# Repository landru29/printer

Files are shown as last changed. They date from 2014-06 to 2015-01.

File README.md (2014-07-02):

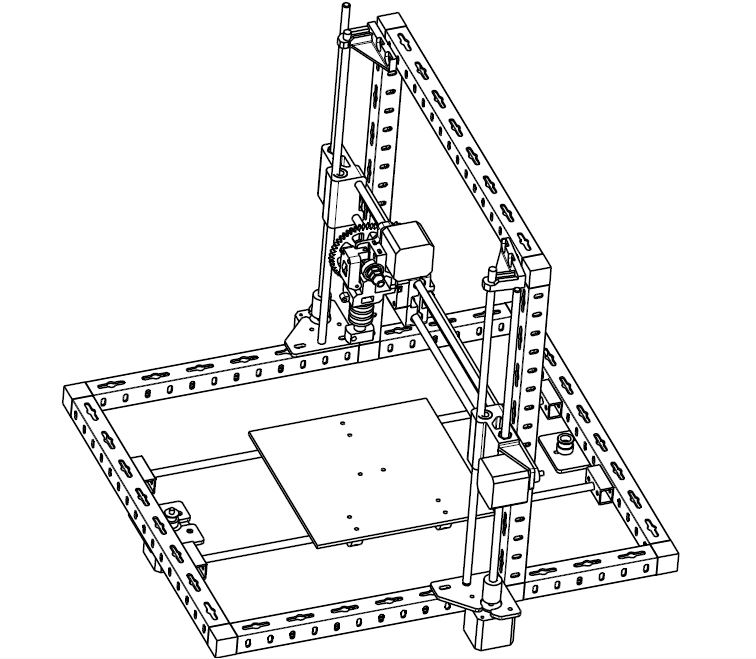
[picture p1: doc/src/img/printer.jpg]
Imprimante 3D


Cadre du projet
===============
Une imprimante 3D est une machine qui permet de reproduire des pièces plus ou moins complexes par apport de matière. Il existe plusieurs types d'imprimantes, selon le principe d'apport de matière utilisé. Le prérimètre de ce projet est une imprimante qui extrude du plastique à déposer couches par couches.

Objectif
========
Le principal objectif est, évidement, de construire une imprimante 3D. Cette imprimante fonctionnera sur le principe d'extrusion de matière plastique. Je m'appuie sur les imprimantes Reprap http://reprap.org/wiki/RepRap/fr. Dans cette perspective, je m'autorise à réutiliser, modifier, adapter des pièces conçues pour d'autres imprimantes Reprap.
Une contrainte forte de ce projet est le budget. En référence, une imprimante Reprap i3 en kit est vendue 450€ sans l'électronique de commande (600€ tout compris). Mon objectif est de limiter mon budget à 250€. C'est difficilement atteignable, mais pas impossible.

Les imprimantes RepRap
======================
Le principe de ces imprimantes est qu'elles sont réplicables. Concrêtement, pour fabriquer une imprimante RepRap, on profite d'une autre imprimante pour imprimer des pièces. Mon projet repose sur ce principe. En effet, pour des questions de facilité (je m'affranchis de certains usinages complexe), la plupart des supports seront imprimés.

Organisation du projet
======================
On trouve deux dossiers:
> * `doc` (documentation du projet, source LaTeX)
> * `mecanical` (conception mécanique du projet)

Doc
---

La documentation est écrite en LaTeX. Pour la regénérer il faut "compiler" les sources. Certaines extensions sont nécessaire à la construction du document (tous ces dépendances se trouvent dans le fichier `doc/source/printer.tex`).
Chaque chapitre a sont propre fichier `*.tex` pour plus de facilité à la rédaction. Un `Makefile` (et un `make.bat`) est à disposition pour faciliter la compilation

Mecanical
---------
Vous trouverez les différents éléments:
> * Les pièces qui devront être imprimées sont dans le dossier `mecanical/to_print`.
> * Les sous-ensembles constituant l'imprimante sont dans `mecanical/assembly`.
> * L'imprimante complete se trouve à la racine de `mecanical`.
> * La bibliothèque de roulement à billes est dans `mecanical/bearing`
> * Les éléments de la structure sont dans `mecanical/tubes`
> * La pré-étude de la tête d'extrusion est dans `mecanical/head`
> * Toute la quincaillerie standard est dans `mecanical/standard`

Attention, il arrive que j'oublie de mettre à jour les fichiers `*.stl` (que je maintiens uniquement pour la visionneuse de GitHub). Vérifiez bien les dates !

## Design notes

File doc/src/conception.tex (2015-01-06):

\section{Conception}
\subsection{Le chassis}
Le chassis est en profile aluminum. Plusieurs solutions se sont %
présentées :\begin{dinglist}{71}%
\item{utiliser du profile pour la construction modulaire}%
\item{utiliser du profile carré}%
\item{utiliser les profiles que propose une célèbre enseigne française %
blanche et verte (fig. \ref{profile} page~\pageref{profile})}
\end{dinglist}%
\par%
\begin{figure}%
   \caption{\label{profile} Profile aluminium 23.5 x 23.5}
   \center{}
\end{figure} %
La première solution est chère. Il faut compter 60\euro{} les trois mètres %
(30mm), sans compter la quincaillerie d'assemblage. \par%
La seconde solution, la moins chère, est plus difficile à mettre en %
oeuvre et nécessite de la précision dans les usinages (perçages, sciages, %
...) pour avoir de bons alignements.\par%
La dernière solution est un bon compromis, car c'est une solution de %
construction modulaire à petit prix (15\euro{} les 2,5m x 25mm). Les jonctions %
se font avec des L et des T en PVC. Si ce n'est pas assez rigide, je %
pourrais encore ajouter des équerres métaliques.
\subsection{L'électronique}
\subsubsection{Spécification}
L'électronique de commande doit respecter les spécifications suivantes: %
\begin{dinglist}{71}%
\item{Elle devra piloter 5 axes (1 X-axis, 1 Y-axis, 2 Z-axis, 1 extrudeur)} %
\item{Elle se connectera à un ordinateur via le port USB} %
\item{Elle supportera une carte SD pour l'imprimante soit autonome lors de %
l'impression} %
\item{Elle saura piloter des moteurs pas à pas bipolaires}
\item{Elle intégrera les différents capteurs (fin de course, température de %
l'extrudeur)}
\item{Elle saura piloter le partie chauffante de l'extrudeur} %
\item{Elle ne sera pas propriétaire} %
\end{dinglist} %
\subsubsection{La Smoothieboard}
Toujours, pour des questions de budget, j'ai écarté la solution Smoothie %
(http://smoothieware.org/smoothieboard). Il faut compter 125\euro{} pour une %
carte 5 axes.
\subsubsection{Arduino}
La solution Arduino consiste à utiliser la version Mega et y brancher une carte %
de commande de moteur. Je suis donc parti sur la configuration suivante: %
\begin{dinglist}{71}%
\item{Freeduino 2650 Mega (un clone de l'Arduino, mais en moins cher): 19\euro}%
\item{RAMPS (une carte de commande de moteur; la plus utilisée par les firmwares %
proposés): 14\euro}%
\item{5 modules A4988 (commande de moteur pas à pas) avec radiateur: 5\euro{} chacun}
\end{dinglist}%
%
\subsection{Liste du matériel}
\csvreader[tabular=|l|l|l|r|,
    table head=\hline & Description & Qte & Prix\\\hline,
    late after line=\\\hline]%
{bom.csv}{Description=\Description,Qte=\Qte,Prix=\Prix}%
{\thecsvrow & \Description & \Qte & \Prix}%
%
\subsection{la tête d'impression}
\noindent Fig. \ref{sch_tete} page~\pageref{sch_tete} \par %
\begin{figure}%
   \caption{\label{sch_tete} Dessin de la tête d'impression}%
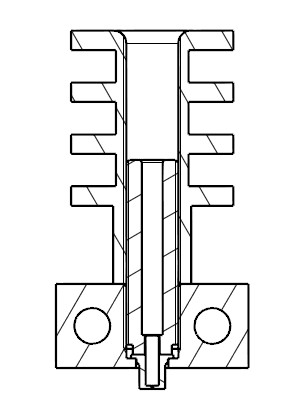
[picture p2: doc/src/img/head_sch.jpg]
   \center{}%
\end{figure}%
La tête d'impression est entièrement fabriquée (fig. \ref{tete_impression} %
page~\pageref{tete_impression}). Elle se compose de quatre éléments:%
\begin{dinglist}{71}%
\item{l'élément de chauffe (qui contiendra la résistance chauffante et la thermistance)}%
\item{le radiateur (qui refroidit la partie haute)}%
\item{le noyau en laiton(pour solidariser le radiateur et l'élément de chauffe)}%
\item{la buse (qui est une partie métalique percée à 0,2mm)}%
\end{dinglist}%
Un noyau en inox (mauvais conducteur thermique) viendra se visser au dessus de la tête.
\begin{figure}%
   \caption{\label{tete_impression} Tête d'impression}%
   \center{}%
\end{figure}%
\subsubsection{L'élément de chauffe}%
\noindent Fig. \ref{sch_chauffe} page~\pageref{sch_chauffe} \par %
\begin{figure}%
   \caption{\label{sch_chauffe} Dessin de l'élément de chauffage}%
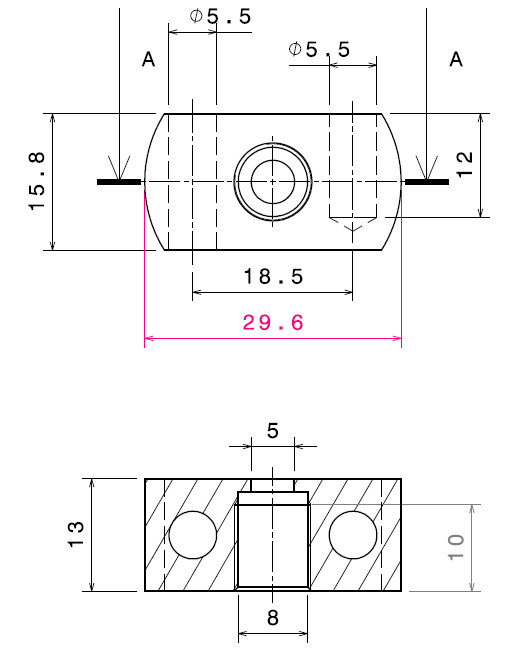
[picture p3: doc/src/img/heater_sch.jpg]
   \center{}%
\end{figure}%
La conception est assez simple. Il faut un bloc de métail (dans mon cas de l'aluminium), et %
percer un logement pour la résistance chauffante et un logement pour la thermistance.%
Pour des facilités d'usinage, je suis parti d'un rond d'aluminium que j'ai fraisé %
(fig. \ref{usinage_chauffe} page~\pageref{usinage_chauffe}).%
\begin{figure}%
   \caption{\label{usinage_chauffe} Usinage de l'élément de chauffage}%
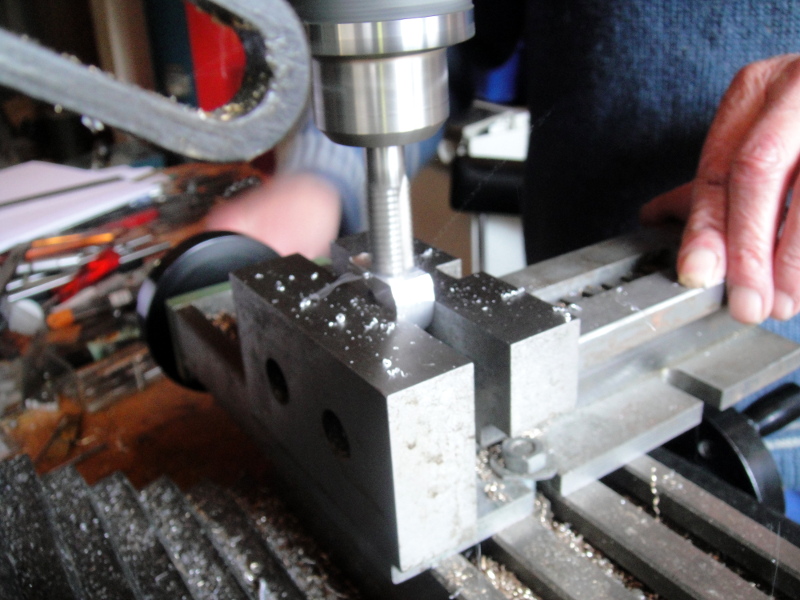
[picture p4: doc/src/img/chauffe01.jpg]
   \center{}%
\end{figure}%
\subsubsection{Le radiateur}%
\noindent Fig. \ref{sch_radiateur} page~\pageref{sch_radiateur} \par %
\begin{figure}%
   \caption{\label{sch_radiateur} Dessin du radiateur}%
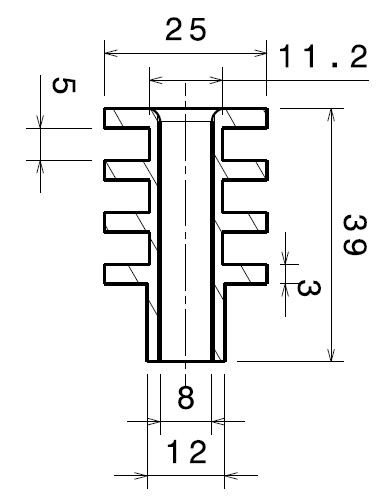
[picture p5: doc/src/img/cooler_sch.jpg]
   \center{}%
\end{figure}%
Cette pièce est aussi en aluminium. Avec un tour j'ai usiné des gorges pour faire les ailettes. %
Le perçage central est taraudé à M8 pour y visser le noyau (fig. \ref{usinage_radiateur} %
page~\pageref{usinage_radiateur}).%
\begin{figure}%
   \caption{\label{usinage_radiateur} Usinage du radiateur}%
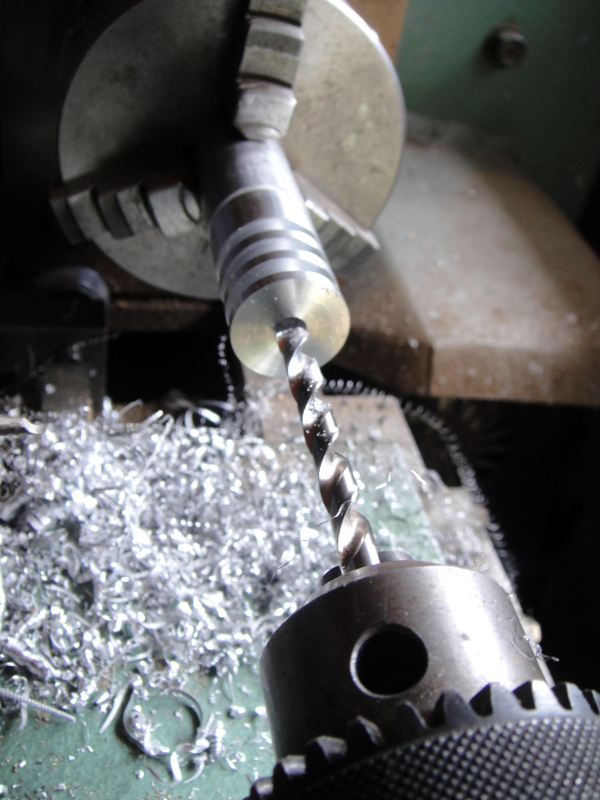
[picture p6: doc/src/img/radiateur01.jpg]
   \center{}%
\end{figure}%
\subsubsection{Le noyau}%
\noindent Fig. \ref{sch_noyau} page~\pageref{sch_noyau} \par %
\begin{figure}%
   \caption{\label{sch_noyau} Dessin du noyau}%
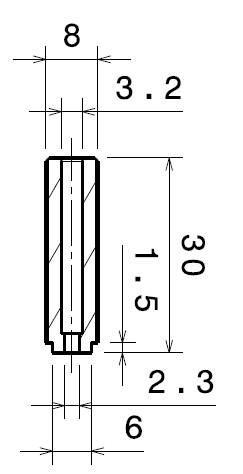
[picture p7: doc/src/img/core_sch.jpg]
   \center{}%
\end{figure}%
Le noyau est fabriqué à partir d'une tige fileté M8 en laiton. Cette pièce est percée à 3,2mm %
pour laisser passer le fil de plastique jusqu'à l'élément de chauffe.%
\subsubsection{La buse}%
Le choix de la buse a été assez difficile. La problématique est la suivante : où trouver %
une partie métallique percée à 0,3mm ou moins, pour pas cher ? \par%
Après renseignement, j'ai vite abandonné l'idée de percer moi-même. Les forêts de très petits %
diamètres sont chers et très fragiles (il faut faire des passes de 0,1mm). %
Je me suis rapidement orienté vers les injecteurs de cyclomoteurs ou de gaz. Les injecteurs de %
cyclomoteurs sont percés gros (minimum 0,6mm). Reste les injecteurs gaz. Chez un chauffagiste %
rennais (\url{http://www.jeanpaulguy.fr/contents/fr/p5656_SD_05447200.html}) j'ai trouvé un injecteur de veilleuse de chaudière murale à gaz (fig. \ref{buse} %
page~\pageref{buse}). C'est une petite pièce à moins de 2\euro{}, percée à 0,28mm ou 0,18mm (%
\url{http://www.jeanpaulguy.fr/contents/fr/p2629.html}).%
\begin{figure}%
   \caption{\label{buse} Buse d'extrusion}%
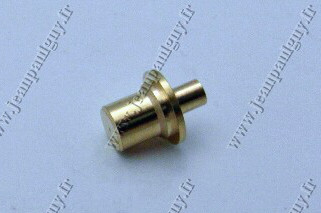
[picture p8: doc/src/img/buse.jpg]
   \center{}%
\end{figure}%
\subsection{La platine assemblée}%
\subsubsection{Fixation des glissières à billes}%
Les glissières à billes sont fixées serrées contre la platine. La fixation est usinée dans un premier temps par tournage, en alésant à 15mm un rond d'aluminium. %
La pièce passe ensuite sur le banc d'une fraiseuse pour réaliser les méplats. L'un des méplats sera tangent à l'alésage (en mangeant 0,3mm, pour assurer le serrage %
de la glissière contre la platine. Les perçages de fixation sont taraudés.
\begin{figure}%
   \caption{\label{bushing-bracket} Fixation de glissière à billes}%
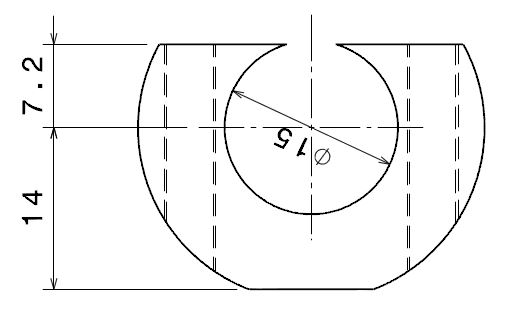
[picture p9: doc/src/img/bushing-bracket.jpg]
   \center{}%
\end{figure}%
\subsubsection{Fixation et contre-fixation de la courroie}%
Cette pièce est réalisée dans de l'aluminium de 6mm d'épaisseur (ce qui correspond à la largeur de la courroie). Pour créer les dentures, il suffit de percer à d1.5mm %
tous les 2mm (le pas de la courroie est de 2mm). Ensuite, scier le long de la ligne de perçage. On accentuera les dents en passant une lime triangulaire. Les %
perçages de fixation sont fraisurés. Le rayon de courbure de 5mm permet de limiter le frottement de la courroie (le retour risque d'être en contact).
\begin{figure}%
   \caption{\label{belt-blocker} Fixation de la courroie}%
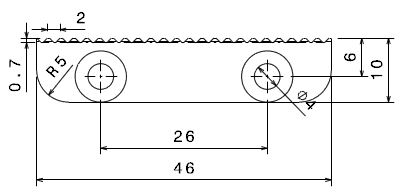
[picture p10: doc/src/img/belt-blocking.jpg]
   \center{}%
\end{figure}%
\subsubsection{Montage}%
Commencer par monter la fixation de courroie 2. Monter, sans serrer la contre-fixation 5. Loger les glissière dans leurs fixations et visser ces dernières sur la %
platine (sans trop serrer pour éviter l'hyperstatisme) avec des vis à têtes fraisurées. Il faudra reprendre la fixation des glissières lorsque la platine sera montée %
sur les stubs (barres de glissement).
\begin{figure}%
   \caption{\label{plate-assy} Montage de la platine}%
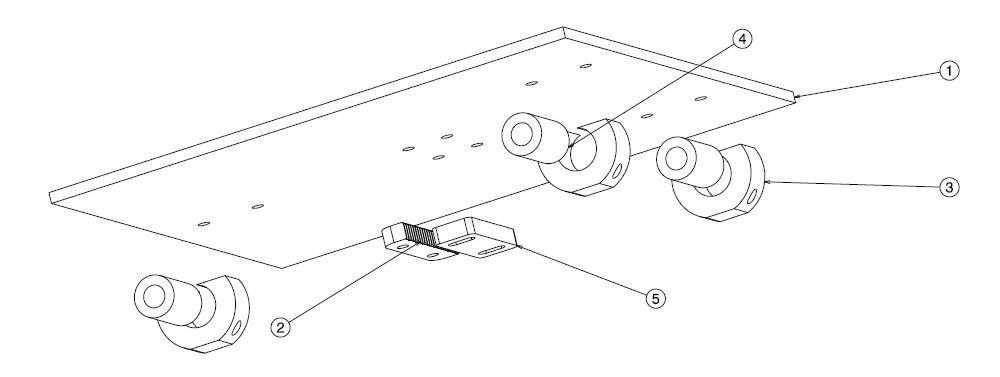
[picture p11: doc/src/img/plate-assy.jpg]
   \center{}%
\end{figure}%
\subsection{Fixation des moteurs}%
Initialement, les moteurs devaient être fixés avec des pièces en platique. Pour des raisons de solidité et de précision, j'ai préféré créer ces pièces en aluminium. %
le centrage des moteurs se fait avec l'alésage de 22mm. Soit cet alésage est réalisé au tour, soit à la lime. Si vous réaliser les alésages au tour, vous n'avez %
pas besoin de les ouvrir à l'extérieur (je l'ai prévu pour laisser passer la lame de scie). Huilez les contacts lors du montage des moteurs afin d'éviter le grippage %
(et abimer les pièces lors d'un prochain démontage). %
La bride de fixation du moteur Y a ses perçages de fixation fraisurés pour assurer un bon contact contre le chassi.
\begin{figure}%
   \caption{\label{y-motor-bracket} Bride de fixation du moteur Y}%
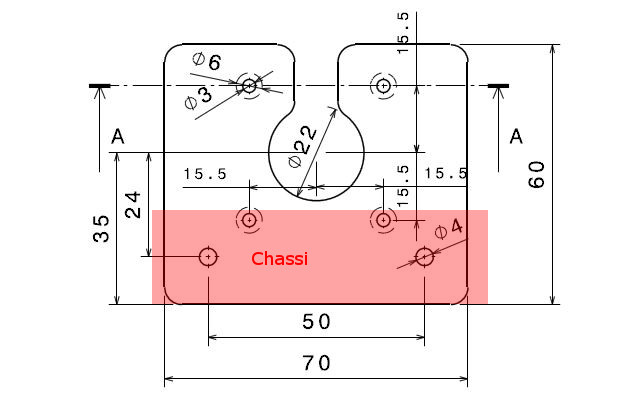
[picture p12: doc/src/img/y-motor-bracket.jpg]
   \center{}%
\end{figure}%

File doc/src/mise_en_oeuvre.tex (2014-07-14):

\section{Mise en oeuvre}%
\subsection{L'électronique}%
\subsubsection{Un jeu de LEGO}
Le montage est relativement simple; la carte RAMPS s'enffiche bien sur la Funduino. %
Il ne faut pas  assembler tout de suite les cartes. Il est préférable de fixer la %
funduino sur son support final (dans mon cas, une tole aluminum en équerre). une fois %
le Funduino fixée, on enffiche  la RAMPS (fig. \ref{montage_carte} %
page~\pageref{montage_carte}). il reste à brancher les commandes de moteur %
sur la RAMPS. Comme indiqué sur le wiki de Reprap, on vérifie les noms des broches et %
on branche (le GND va sur le GND et le direction va sur direction).%
\begin{figure}%
   \caption{\label{montage_carte} Montage de RAMPS sur la Funduino}%
   \center{}%
\end{figure}%
\subsubsection{Alimentation externe} %
Il faut maintenant l'alimentation externe sur la RAMPS (bornier vert à quatre broches). %
Il est préconisé d'alimenter en 12V. J'ai donc utilisé une alimentation de PC (500W, %
qui peut le plus, peu le moins). Pour info, le 0V, c'est le fil noir, le 12V, c'est le %
fil jaune. Comme d'habitude, l'alimentation de PC est un élément que j'ai trouvé %
dans un vide-grenier (5\euro{}). Il y a une entrée 5A et une entrée 11A. Mon %
alimentation a une capacité de 18A sur la sortie 12V. Il m'a donc suffit de mettre %
les deux entrées en parallèle sur le 12V fig. \ref{alimentation} %
page~\pageref{alimentation}).%
\begin{figure}%
   \caption{\label{alimentation} Branchement de l'alimentation externe}%
   \center{}%
\end{figure}%
\subsubsection{Les premières embuches}
Ce qui devait arriver arriva. En faisant des essais sur la carte RAMPS, j'ai fait un %
court-circuit (5v relié au 0V). Une seconde a suffit pour que de la fumée s'échappe %
de la Funduino. Une %
fois l'ensemble démonté, un composant avait pris copieux. \par %
Diagnostique : quand je branche seul, le Funduino au PC avec le cordon USB, le %
périphérique est reconnu. Si maintenant, j'alimente la RAMPS en 12V, le PC perd la %
connection USB. C'est embêtant. Dans ces cas là, il faut garder son calme. La %
Funduino, tout comme l'Arduino est une carte super simple : il y a un micro controlleur, %
quelques résistances, un condensateur, parfois une interface USB (sinon, pris en charge %
par le micro controlleur), et ... un régulateur de tension (AMS1117). Ce régulateur de %
tension permet de garder 5V dans le circuit quelque soit la tension d'alimentation (tant %
qu'elle reste au dessus de 5V). C'est un composant à trois pattes équipé d'un radiateur, qui %
ressemble à une quatrième patte (fig. \ref{regulator} page~\pageref{regulator}). %
\begin{figure}%
   \caption{\label{regulator} Régulateurs de tension}%
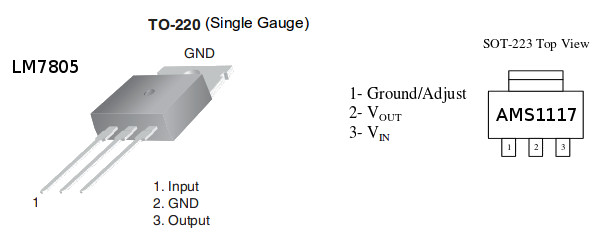
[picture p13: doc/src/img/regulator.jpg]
   \center{}%
\end{figure}%
\begin{figure}%
   \caption{\label{arduino_principle} Schéma de principe du Funduino}%
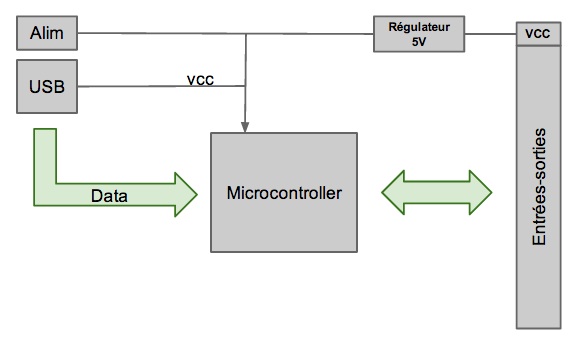
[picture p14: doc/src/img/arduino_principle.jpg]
   \center{}%
\end{figure}%
En regardant bien, c'est ce composant qui a chargé. %
En regardant le schéma de la figure \ref{arduino_principle} en page~\pageref{arduino_principle}, %
on comprend bien pourquoi le Funduino fonctionnait avec l'alimentation USB, et ne %
fonctionnait plus avec une alimentation externe. \par%
La réparation est simple : le LM7805 rempli la même fonction. Il est carrément plus gros, %
mais, on va trouver à le loger. J'en ai un sous le coude, c'est parti. Il faut être %
vigilent sur l'ordre des pattes. Pour s'adapter au circuit, il faut croiser le OUT %
et le GND pour avoir dans l'ordre [IN OUT GND] (fig. \ref{regulator} page~\pageref{regulator}). Ensuite on soude (fig. \ref{funduino_repared} %
page~\pageref{funduino_repared}). J'ai pris soin de mettre un scotch sur le radiateur du %
LM7805 pour éviter que la partie métallique ne touche une autre partie de la Funduino.\par{} %
Je rebranche le tout, et ... c'est reparti comme en 40 ! Ce qu'il faut retenir, c'est %
que la Funduino est très fragile (en même temps, un court-circuit ne pardonne pas), %
et qu'il faut vérifier à deux fois avant de brancher quelque chose (on ne branchera %
rien à chaud !).%
\begin{figure}%
   \caption{\label{funduino_repared} Funduino avec son nouveau régulateur de tension}%
   \center{}%
\end{figure}%
\subsection{Réglage des controlleurs de moteurs}
\subsubsection{Principe du réglage}
Vous avez dû remarquer que sur chaque contrôleur A4988, il y a un potentiomètre. Il sert %
à quelque chose. En fait, le composant A4988 est pourvu d'un régulateur de courant. \c{C}a tombe %
bien, les moteurs que j'ai achetés (42BYGHW609) ont un ampérage maximum de 1,7A. Nous allons %
donc agir sur ce potentiomètre pour que l'intensité de sortie ne dépasse pas 1,7A.
\subsubsection{Câblage du module}
Nous allons faire un petit banc de test pour régler nos modules (fig. \ref{a4988_wired} %
page~\pageref{a4988_wired}). Procédez ainsi:\begin{dinglist}{71}%
\item{Branchez GND sur le 0V de l'Arduino}%
\item{Branchez VDD sur le 5V de l'Arduino}%
\item{Branchez /RESET et /SLEEP sur 5V}
\item{Branchez /ENABLE sur la pin 13 de l'Arduino}
\item{Branchez STEP sur la pin 12 de l'Arduino}
\item{Branchez DIR sur la pin 11 de l'Arduino}
\item{Branchez VMOT sur le 12V de l'alimentation externe (alimentation d'ordinateur)}
\item{Branchez un bobinage moteur sur 1A, 1B}
\item{Branchez l'autre bobinage moteur sur 2A, 2B}
\end{dinglist}%
Pour trouver un bobinage moteur, sans alimentation, reliez deux broches du moteur et tounez l'axe %
à la main; s'il y a une petite résistance à la rotation, c'est que vous avez courcircuité un bobinage %
(c'est dû aux courants de Foucault). Sinon, testez une autre paire%
\begin{figure}%
   \caption{\label{a4988_wired} câblage du A4988}%
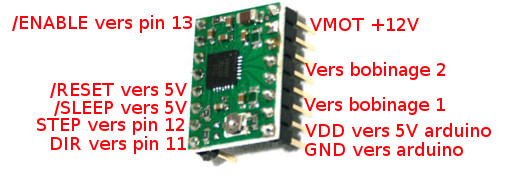
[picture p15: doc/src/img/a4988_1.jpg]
   \center{}%
\end{figure}%
\subsubsection{Le test}
Insésez un ampèremètre dans le circuit d'un bobinage (l'ampèremètre se branche en série), et chargez %
le programme suivant dans l'arduino:
\begin{verbatim}
/*
Test moteur PAP (pas entier)
Carte Pololu avec puce A4988 + régulateur de tension > 
http://www.pololu.com/catalog/product/1183
Ch.Aubert Déc.2011
*/

/************** Définition des E/S *************************/
const int dirPin = 11;  // DIR
const int stepPin = 12; // STEP
const int enablePin = 13; // ENABLE

void setup()
{
  pinMode(stepPin, OUTPUT); // Dir et Step en sortie
  pinMode(dirPin, OUTPUT);
  pinMode(enablePin, OUTPUT); // broche Enable en sortie
  digitalWrite(enablePin, HIGH);

  calibrate(); // lance le stall moteur Ampérage max !
  //test(); // lance le test !!
}

void loop()
{
  // rien pour l'instant !
}

void calibrate() // Stall moteur Ampérage max !
{
  digitalWrite(enablePin, LOW);
}

void test() //  faire tourner le moteur 200 pas
{
  int j;
  digitalWrite(enablePin, LOW);
  delayMicroseconds(2);

  digitalWrite(dirPin, HIGH);
  for(j=0; j<=199; j++) {
    delay(200);
    digitalWrite(stepPin, LOW);
    delayMicroseconds(10);
    digitalWrite(stepPin, HIGH);
    delayMicroseconds(1000);
  }
  digitalWrite(enablePin, HIGH); 
}
\end{verbatim}
\begin{figure}%
   \caption{\label{a4988_montage} câblage du A4988}%
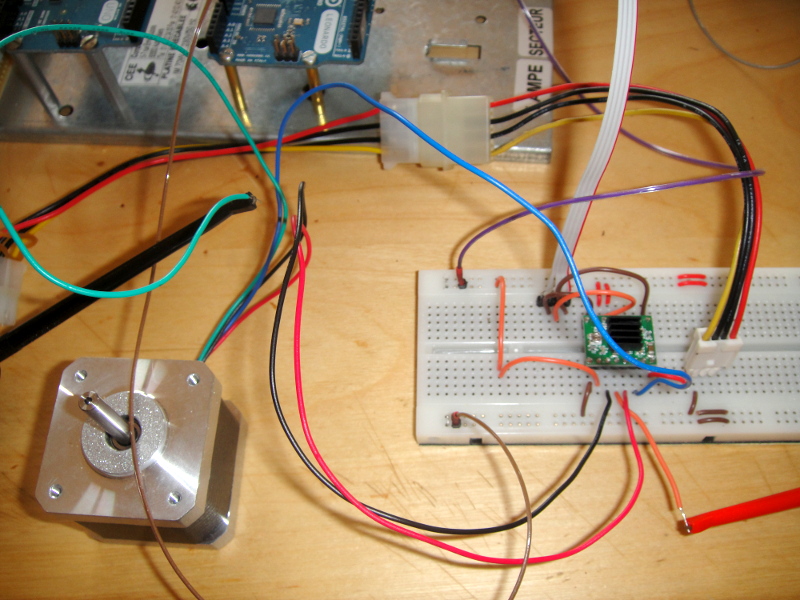
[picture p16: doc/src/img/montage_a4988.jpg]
   \center{}%
\end{figure}%
\begin{figure}%
   \caption{\label{a4988_ampere} câblage du A4988}%
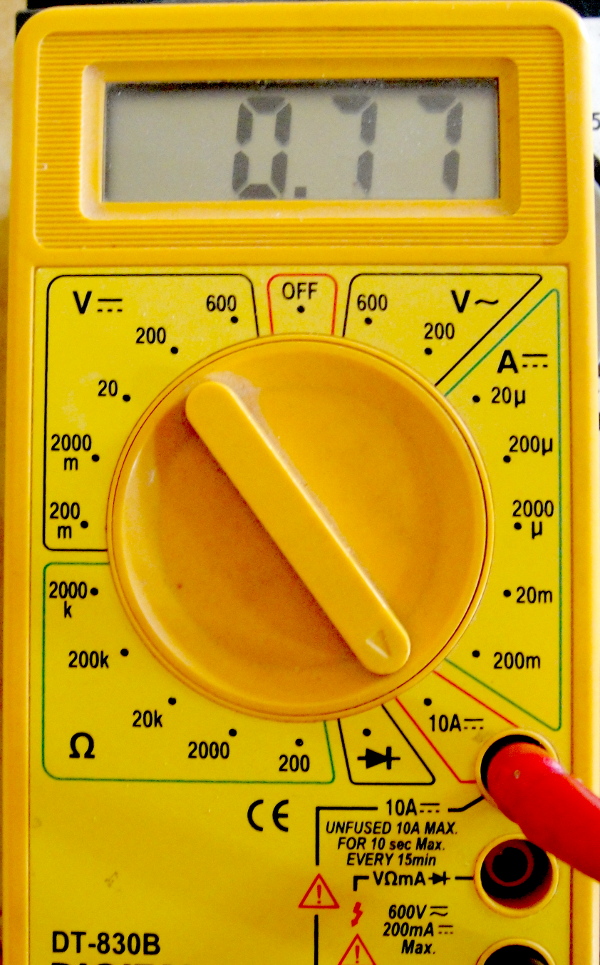
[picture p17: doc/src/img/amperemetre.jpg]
   \center{}%
\end{figure}%
Alimentez l'arduino (par le cable USB), et branchez l'alimentation. Attention, on ne décâble jamais %
le moteur lorsque les alimentations (arduino et alim externe de 12V) sont en marche. Par l'effet de %
courants induits, un retour de courant pourrait détruire votre contrôleur. Normalement, le moteur %
ne tourne pas, mais l'axe est rigide. \\%
N'utilisez pas de tournevis à manche métalique; j'ai remarqué que les mesures sont faussées. Tournez le %
potentiomètre pour ne pas dépasser 0,7 courant max (1,2A pour ma part). J'ai fait le choix de brider %
à 0,8A (fig. \ref{a4988_ampere} page~\pageref{a4988_ampere}). %

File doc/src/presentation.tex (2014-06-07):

\section{Présentation}
\subsection{Cadre du projet}
Une imprimante 3D est une machine qui permet de reproduire des pièces %
plus ou moins complexes par apport de matière. Il existe plusieurs types %
d'imprimantes, selon le principe d'apport de matière utilisé. Le prérimètre %
de ce projet est une imprimante qui extrude du plastique à déposer couches %
par couches.
%
\subsection{Objectif}
Le principal objectif est, évidement, de construire une imprimante 3D. Cette %
imprimante fonctionnera sur le principe d'extrusion de matière plastique. Je %
m'appuie sur les imprimantes Reprap (\url{http://reprap.org/wiki/RepRap/fr}). %
Dans cette perspective, je m'autorise à réutiliser, modifier, adapter des pièces %
conçues pour d'autres imprimantes Reprap.\par%
%
Une contrainte forte de ce projet est le budget. En référence, une imprimante %
Reprap i3 en kit est vendue 450\euro{} sans l'électronique de commande (600\euro{} tout %
compris). Mon objectif est de limiter mon budget à 250\euro{}. C'est difficilement %
atteignable, mais pas impossible.
%
\subsection{Les imprimantes RepRap}
Le principe de ces imprimantes est qu'elles sont réplicables. Concrêtement, %
pour fabriquer une imprimante RepRap, on profite d'une autre imprimante pour imprimer %
des pièces. Mon projet %
repose sur ce principe. En effet, pour des questions de facilité (je m'affranchis %
de certains usinages complexe), la plupart des supports seront imprimés.

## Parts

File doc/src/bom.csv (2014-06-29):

Description | Qte | Prix
V modulaire | 6 | 6.60 \euro
T modulaire | 2 | 2.80 \euro
Tube alu modulaire 23.5 | 3.0 | 21.60 \euro
Carte RAMPS | 1 | 14.00 \euro
Commande moteur A4988 | 5 | 23.00 \euro
Funduino 2650 Mega | 1 | 19.00 \euro
Roulements linéaires LM8UU | 12 | 6.70 \euro
Courroie GT2 (2m) + 2 poulies | 1 | 7.00 \euro
Moteur pas à pas nema17 | 5 | 50.00 \euro
Rond inox 8mm | 3 | 20.00 \euro
Injecteur SD05447200 / SD05447000 | 1 | 2.00 \euro
Alimentation PC 500W | 1 | 10.00 \euro
Résistance 5.6(5W) / CTN 100k | 1 | 1.00 \euro
Coupleur 5x8 | 2 | 2.00 \euro
Quincaillerie | 1 | 10.00 \euro
Total |  | 195.70 \euro

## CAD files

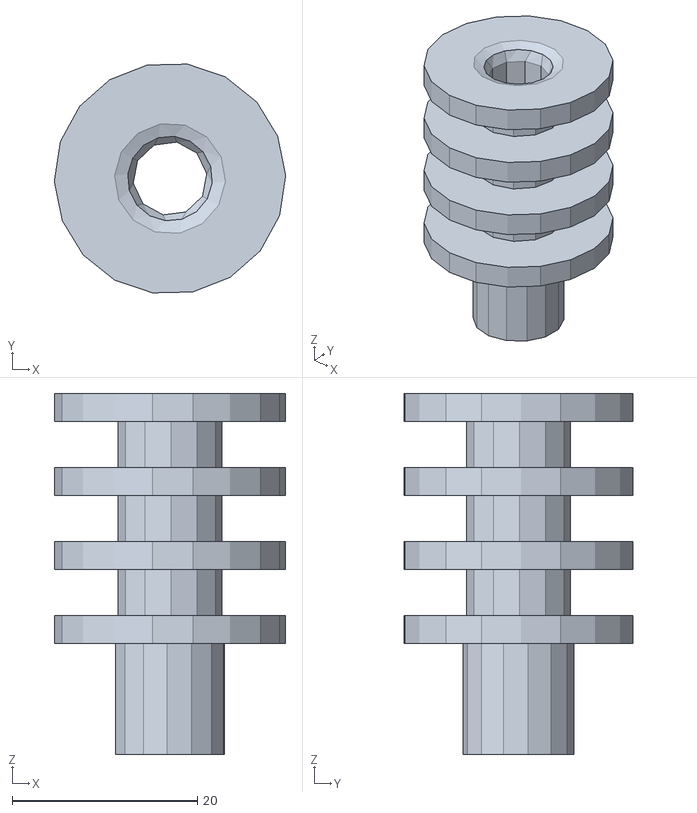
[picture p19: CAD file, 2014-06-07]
mecanical/head/cooler.stl
25.0 x 24.7 x 39.0

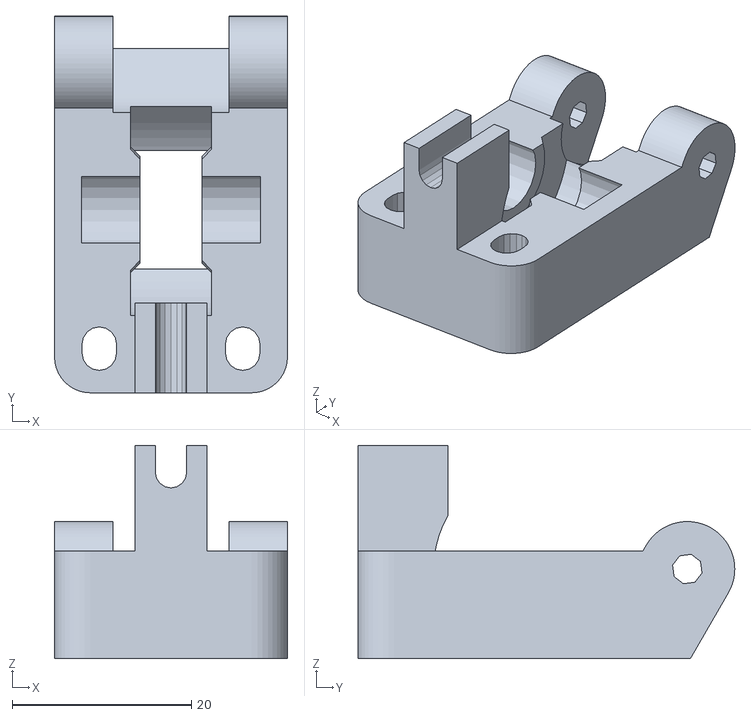
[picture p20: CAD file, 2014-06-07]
mecanical/import/Prusa_Mendel_i3_Rework/EXTRUDER-IDLER-avec-guide.stl
26.0 x 42.0 x 23.8

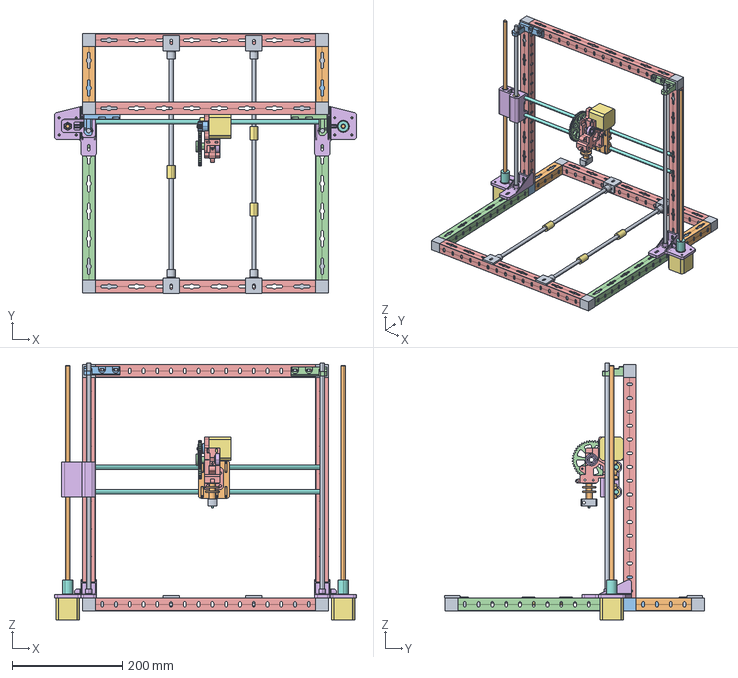
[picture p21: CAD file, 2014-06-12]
mecanical/printer.stp
548.0 x 471.0 x 466.0 mm

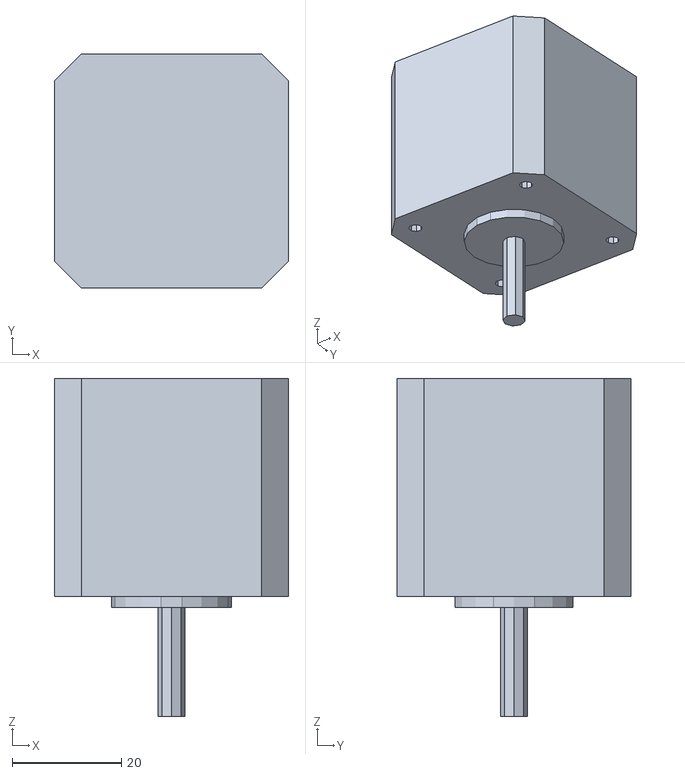
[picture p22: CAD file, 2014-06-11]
mecanical/standard/Motor.stl
43.0 x 43.0 x 62.0

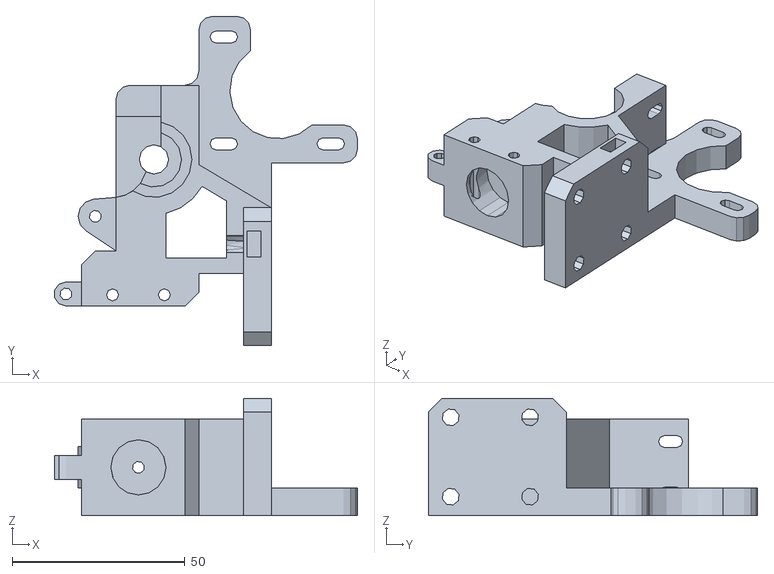
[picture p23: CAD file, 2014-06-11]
mecanical/tmp/extruder_bracket.stl
87.8 x 95.5 x 34.0

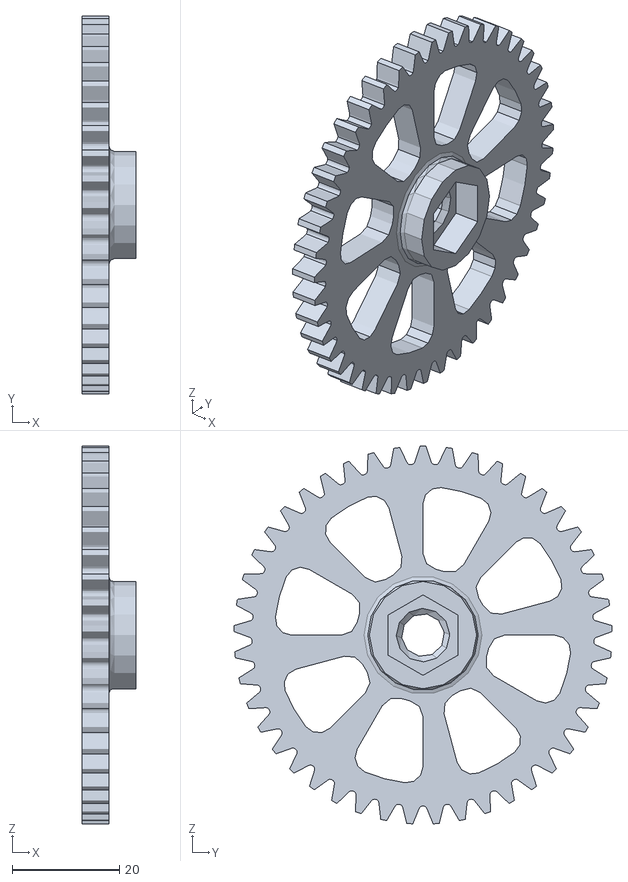
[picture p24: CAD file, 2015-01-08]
mecanical/to_print/big_gear.stl
10.0 x 70.5 x 70.4

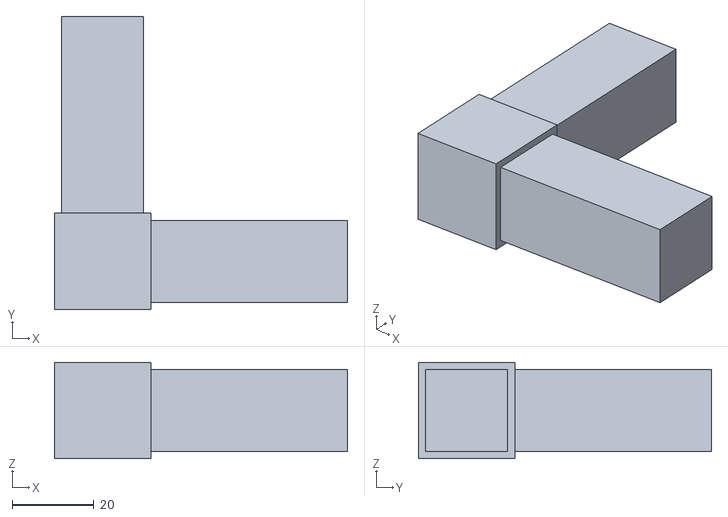
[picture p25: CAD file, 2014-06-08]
mecanical/tubes/L.stl
71.5 x 71.5 x 23.5

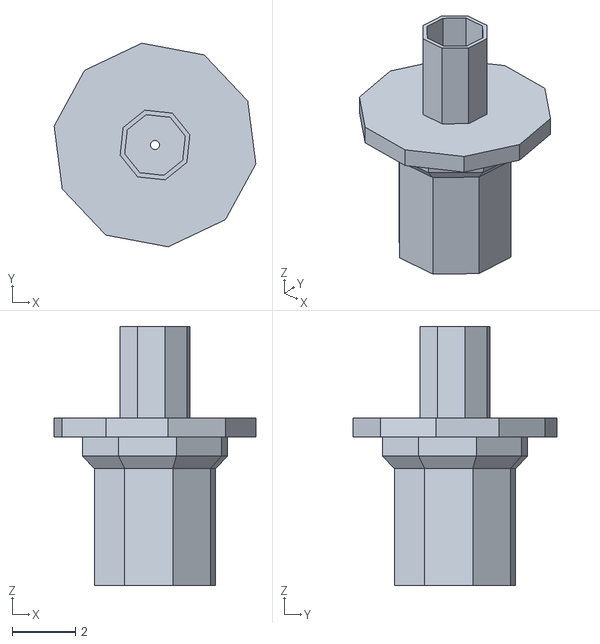
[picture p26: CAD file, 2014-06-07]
mecanical/head/printing_nozzle.stl
6.39 x 6.45 x 8.20

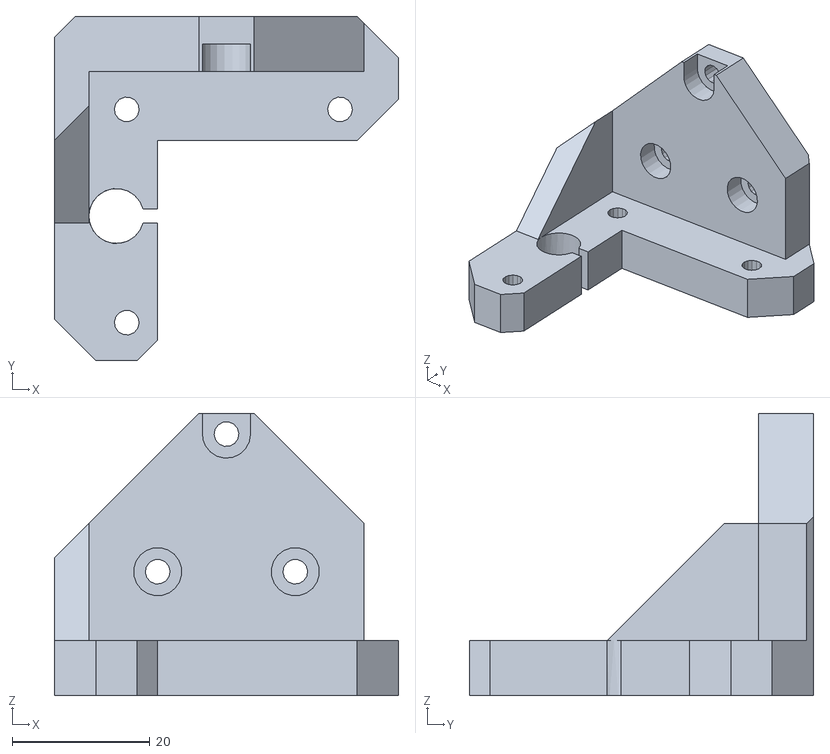
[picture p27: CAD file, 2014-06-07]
mecanical/import/Prusa_Mendel_i3_Rework/Z-AXIS-BOTTOM-RIGHT-V2.stl
50.0 x 50.0 x 41.0

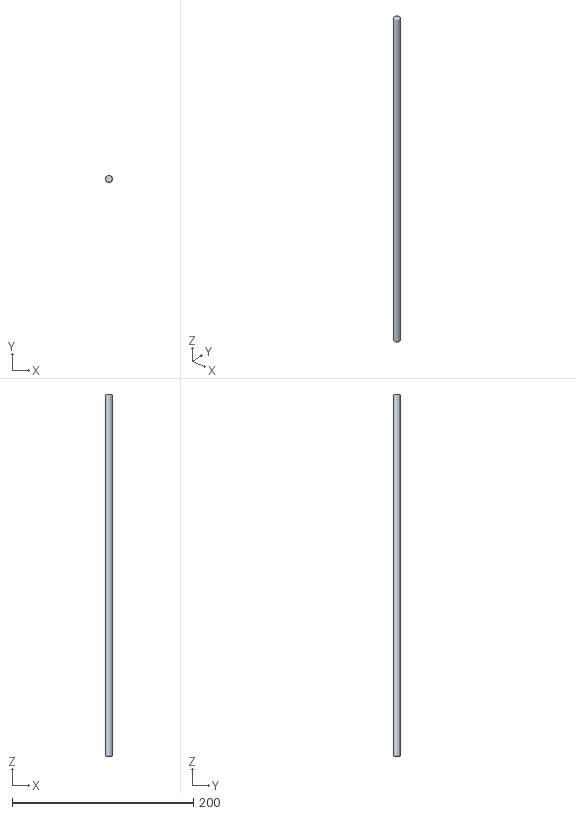
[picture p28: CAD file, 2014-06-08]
mecanical/standard/vis.stl
8.00 x 7.61 x 400.0

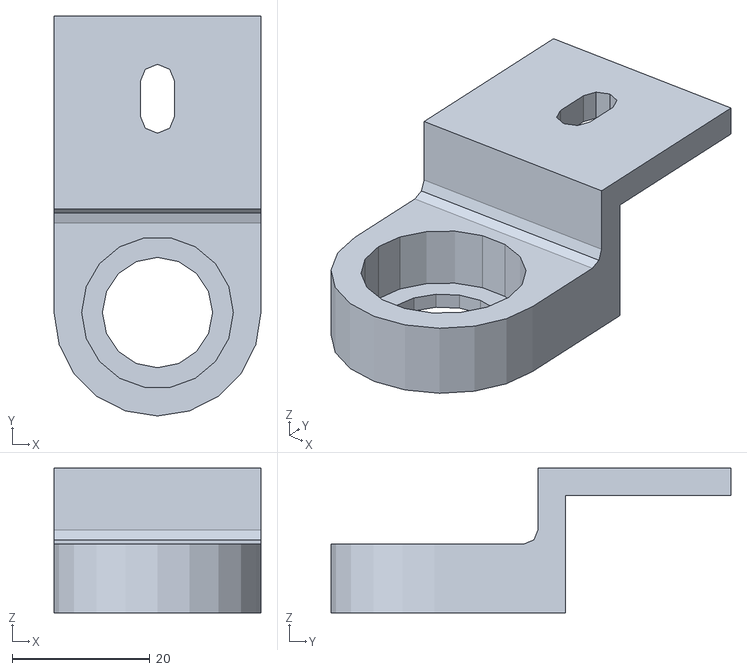
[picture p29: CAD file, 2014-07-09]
mecanical/to_print/Y_idler.stl
30.0 x 58.0 x 21.0

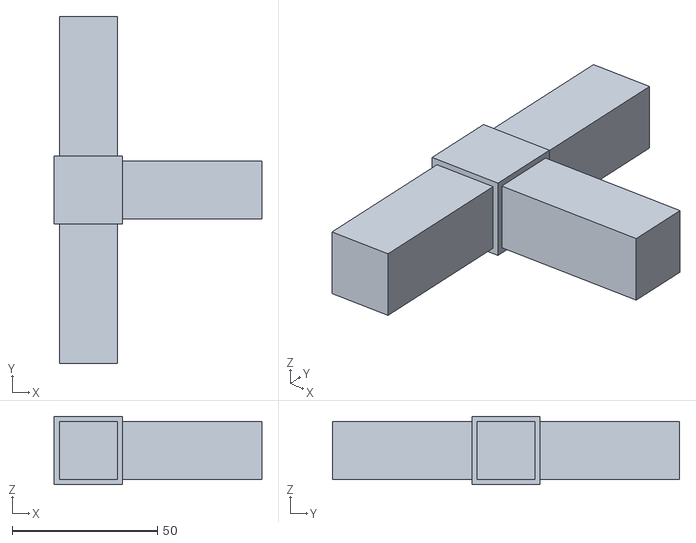
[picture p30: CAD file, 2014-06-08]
mecanical/tubes/T.stl
71.5 x 119.5 x 23.5

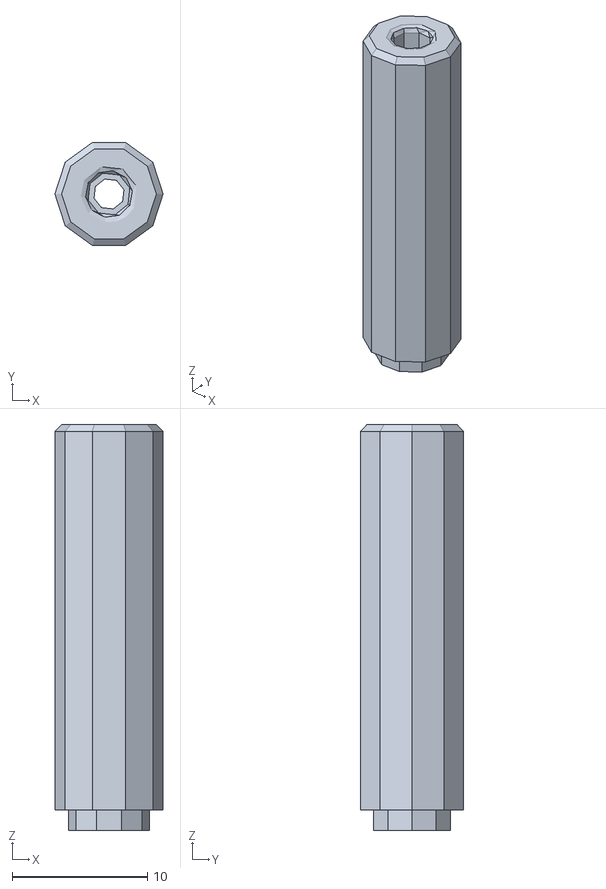
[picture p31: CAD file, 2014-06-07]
mecanical/head/core.stl
8.00 x 7.61 x 30.0

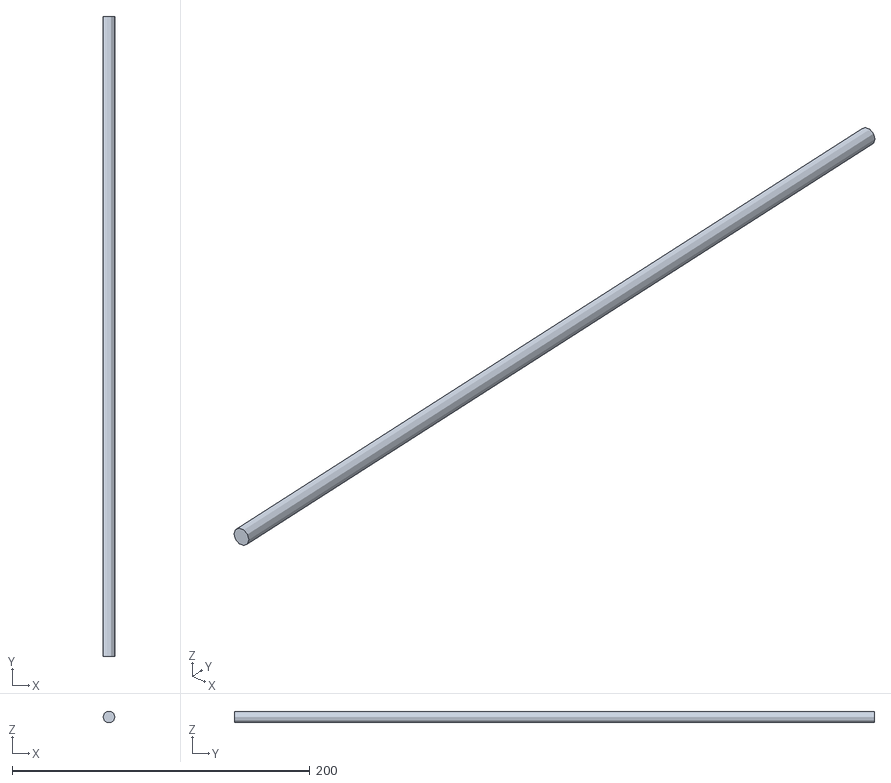
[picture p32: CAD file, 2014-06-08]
mecanical/standard/Stub_X.stl
8.00 x 430.0 x 7.61

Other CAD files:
mecanical/import/Prusa_Mendel_i3_Rework/BODY-EXTRUDEUR-WADE.stl
mecanical/to_print/belt-bracket.stl
mecanical/tubes/profile_150_Y.stl
mecanical/head/heater.stl
mecanical/aluminium-sheet/plate.CATPart
mecanical/aluminium-sheet/y-belt-blocker.CATPart
mecanical/aluminium-sheet/y-belt-press.CATPart
mecanical/aluminium-sheet/y-motor-bracket.CATPart
mecanical/aluminium-sheet/y-stub-bracket.CATPart
mecanical/aluminium-sheet/y-tensioner.CATPart
mecanical/aluminium-sheet/z-motor-bracket.CATPart
mecanical/aluminium-sheet/z-stub-bracket.CATPart
mecanical/assembly/X_Carriage.CATProduct
mecanical/assembly/body.CATProduct
mecanical/assembly/extruder.CATProduct
mecanical/assembly/head.CATProduct
mecanical/assembly/plate-assy.CATProduct
mecanical/assembly/pulley.CATProduct
mecanical/assembly/y-motor.CATProduct
mecanical/assembly/y_carriage.CATProduct
mecanical/assembly/z_carriage.CATProduct
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

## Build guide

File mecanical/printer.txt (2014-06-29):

txt format Save for document C:\Users\Cyrille\Documents\GitHub\printer\mecanical\printer.CATProduct 
--------------------------------------------------------------------------------------------------- 

RootProduct : Produit1 
  | 
  |- Product : Body (Body.1) 
        | 
        |- Product : L (L.1) 
        | 
        |- Product : L (L.2) 
        | 
        |- Product : L (L.3) 
        | 
        |- Product : L (L.4) 
        | 
        |- Product : profile 150 (profile 150.1) 
        | 
        |- Product : profile 150 (profile 150.2) 
        | 
        |- Product : T (T.1) 
        | 
        |- Product : T (T.2) 
        | 
        |- Product : profile 300 (profile 300.1) 
        | 
        |- Product : profile 300 (profile 300.2) 
        | 
        |- Product : profile 400 Z (profile 400 Z.1) 
        | 
        |- Product : profile 400 Z (profile 400 Z.2) 
        | 
        |- Product : profile 400 (profile 400.1) 
        | 
        |- Product : profile 400 (profile 400.2) 
        | 
        |- Product : profile 400 (profile 400.3) 
        | 
        |- Product : L (L.5) 
        | 
        |- Product : L (L.6) 
  | 
  |- Product : z_motor_left (z_motor_left.1) 
        | 
        |- Product : Motor-Support-bottom-left (Motor-Support-bottom-left.1) 
        | 
        |- Product : Motor (Motor.1) 
        | 
        |- Product : coupling (coupling.1) 
        | 
        |- Product : stub_Z (stub_Z.1) 
        | 
        |- Product : vis (vis.1) 
        | 
        |- Product : Z-Axis-Top-Left (Z-Axis-Top-Left.1) 
  | 
  |- Product : z_motor_right (z_motor_right.1) 
        | 
        |- Product : vis (vis.1) 
        | 
        |- Product : Motor_Support_bottom_right (Motor_Support_bottom_right.1) 
        | 
        |- Product : Motor (Motor.1) 
        | 
        |- Product : coupling (coupling.1) 
        | 
        |- Product : stub_Z (stub_Z.1) 
        | 
        |- Product : Z-Axis-Top-Right (Z-Axis-Top-Right.1) 
  | 
  |- Product : z_carriage (z_carriage.1) 
        | 
        |- Product : Nut8 (Nut8.1) 
        | 
        |- Product : Nut8 (Nut8.2) 
        | 
        |- Product : Z_carriage_left (Z_carriage_left.1) 
        | 
        |- Product : Bushing (Bushing.1) 
        | 
        |- Product : Bushing (Bushing.2) 
        | 
        |- Product : Stub_Y (Stub_Y.1) 
        | 
        |- Product : Stub_Y (Stub_Y.2) 
        | 
        |- Product : Z_carriage_right (Z_carriage_right.1) 
        | 
        |- Product : Bushing (Bushing.3) 
        | 
        |- Product : Bushing (Bushing.4) 
        | 
        |- Product : Nut8 (Nut8.3) 
        | 
        |- Product : Nut8 (Nut8.4) 
        | 
        |- Product : Motor (Motor.1) 
        | 
        |- Product : bearing10 8 (bearing10 8.1) 
  | 
  |- Product : y_carriage (y_carriage.1) 
        | 
        |- Product : stub X (stub X.1) 
        | 
        |- Product : stub X (stub X.2) 
        | 
        |- Product : Bushing (Bushing.1) 
        | 
        |- Product : Bushing (Bushing.2) 
        | 
        |- Product : Bushing (Bushing.3) 
        | 
        |- Product : support stub (support stub.1) 
        | 
        |- Product : support stub (support stub.2) 
        | 
        |- Product : support stub (support stub.3) 
        | 
        |- Product : support stub (support stub.4) 
        | 
        |- Product : triangle (triangle.1) 
        | 
        |- Product : Y-idler (Y-idler.1) 
        | 
        |- Product : bearing10 8 (bearing10 8.1) 
  | 
  |- Product : X_Carriage (X_Carriage.1) 
        | 
        |- Product : X_carriage (X_carriage.1) 
        | 
        |- Product : Bushing (Bushing.1) 
        | 
        |- Product : Bushing (Bushing.2) 
        | 
        |- Product : Bushing (Bushing.3) 
        | 
        |- Product : Bushing (Bushing.4) 
        | 
        |- Product : X_carriage_cover (X_carriage_cover.1) 
  | 
  |- Product : Extruder (Extruder.1) 
        | 
        |- Product : Small_gear (Small_gear.1) 
        | 
        |- Product : Big_gear (Big_gear.1) 
        | 
        |- Product : Motor (Motor.1) 
        | 
        |- Product : extruder_bracket (extruder_bracket.1) 
        | 
        |- Product : bearing10 8 (bearing10 8.1) 
        | 
        |- Product : bearing10 8 (bearing10 8.2) 
        | 
        |- Product : tete (tete.1) 
              | 
              |- Product : core (core.1) 
              | 
              |- Product : printing nozzle (printing nozzle.1) 
              | 
              |- Product : heater (heater.1) 
              | 
              |- Product : radiateur (radiateur.1) 
              | 
              |- Product : core_stainless (core_stainless.1) 
        | 
        |- Product : screw8_60 (screw8_60.1) 
        | 
        |- Product : Nut8 (Nut8.1) 
        | 
        |- Product : Nut8 (Nut8.2) 
        | 
        |- Product : Nut8 (Nut8.3) 
        | 
        |- Product : extruder_idler (extruder_idler.1) 
        | 
        |- Product : bearing10 8 (bearing10 8.3) 
        | 
        |- Product : idler_core (idler_core.1)

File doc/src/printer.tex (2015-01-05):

\documentclass[a4paper,12pt]{article}%
\usepackage[utf8]{inputenc}%
\usepackage[francais]{babel}%
\usepackage[T1]{fontenc}%
\usepackage{eurosym}%
\usepackage{csvsimple}%
\usepackage{pifont}%
\usepackage{graphicx}%
\usepackage[pdftex,%
    pdfauthor={C. Meichel},%
    pdftitle={3D-Printer},%
    pdfsubject={Conception d'une imprimante 3D},%
    pdfkeywords={reprap,printer},%
    pdfproducer={Latex},%
    pdfcreator={pdflatex}]{hyperref}%
\usepackage{float}%
%\floatstyle{boxed}%
\restylefloat{figure}%
%
\author{C. Meichel}%
\title{3D-Printer}%
\date{\today}%
%
\begin{document}%
%
%
%
%
%
%
%
\maketitle%
%
\clearpage%
\tableofcontents%
\clearpage%
%
\input{presentation}%
\input{conception}%
\input{mise_en_oeuvre}%
%
\clearpage%
\listoffigures%
%
\end{document}%

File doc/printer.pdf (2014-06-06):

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

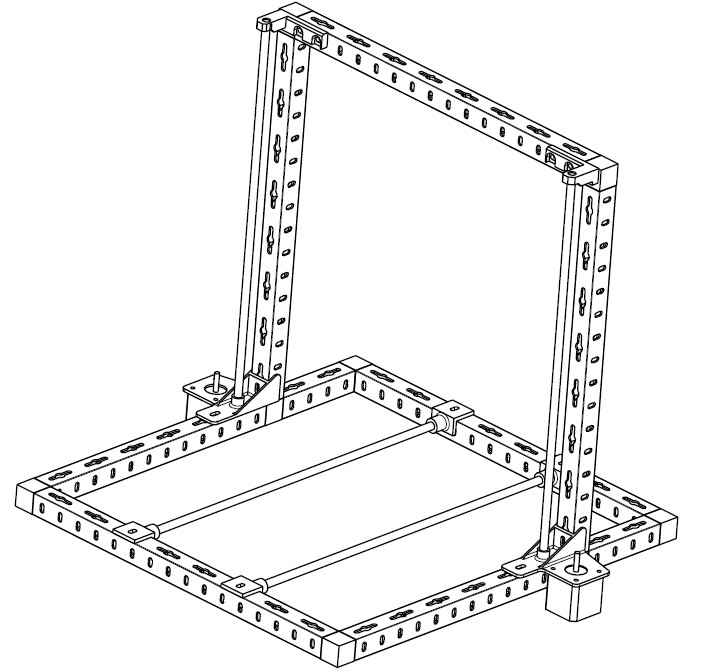
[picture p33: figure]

## Table des matières

1 Présentation | 3
2 Conception | 3
3 Mise en oeuvre | 6

2

1 | Présentation
1.1 | Cadre du projet

Une imprimante 3D est une machine qui permet de reproduire des pièces plus ou moins complexes par apport de matière. Il existe plusieurs types d'imprimantes, selon le principe d'apport de matière utilisé. Le prérimètre de ce projet est une imprimante qui extrude du plastique à déposer couches par couches.

### 1.2 Objectif

Le principal objectif est, évidement, de construire une imprimante 3D. Cette imprimante fonctionnera sur le principe d'extrusion de matière plastique. Je m'appuie sur les imprimantes Reprap (http://reprap.org/wiki/RepRap/fr). (http://reprap.org/wiki/RepRap/fr) Dans cette perspective, je m'autorise à réutiliser, modier, adapter des pièces conçues pour d'autres imprimantes Reprap.Une contrainte forte de ce projet est le budget. En référence, une imprimante Reprap i3 en kit est vendue 450e sans l'électronique de commande (600e tout compris). Mon objectif est de limiter mon budget à 200e. C'est dicilement atteignable, mais pas impossible.

### 1.3 Les imprimantes RepRap

Le principe de ces imprimantes est qu'elles sont réplicables. Concrêtement, pour fabriquer une imprimante RepRap, il faut imprimer des pièces. Mon projet repose sur ce principe. En eet, pour des questions de facilité (je m'aranchis de certains usinages complexe), la plupart des supports seront imprimés.

2 | Conception
2.1 | Le chassis

Le chassis est en prole aluminum. Plusieurs solutions se sont présentées : utiliser du prole pour la construction modulaire
utiliser du prole carré
utiliser les proles que propose une célèbre enseigne française blanche
| et verte (g. 1 page 4)
La première solution est chère. Il faut compter 60eles trois mètres (30mm), sans compter la quincaillerie d'assemblage.
| 3

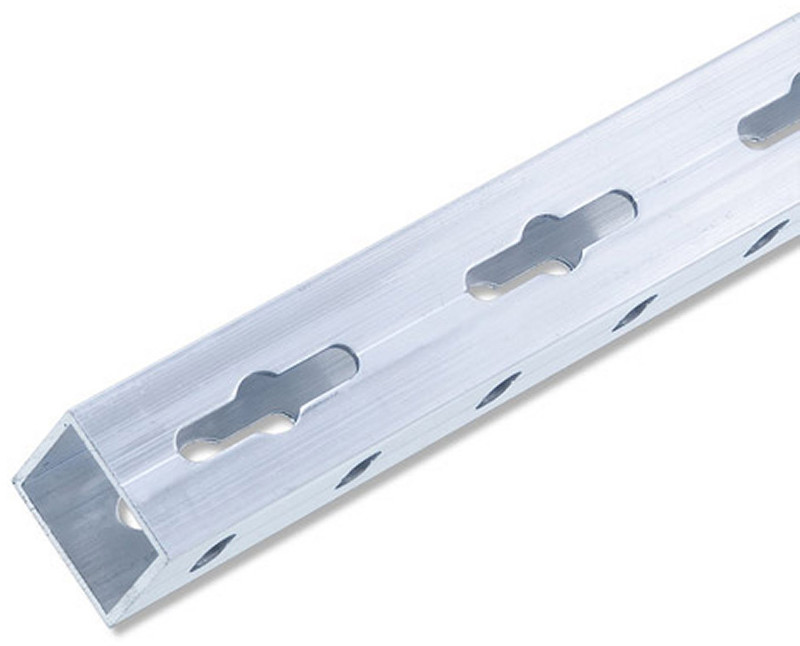
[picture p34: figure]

Figure 1: prole aluminium 23.5 x 23.5

La seconde solution, la moins chère, est plus dicile à mettre en oeuvre et nécessite de la précision dans les usinages (perçages, sciages, ...) pour avoir de bons alignements.La dernière solution est un bon compromis, car c'est une solution de construction modulaire à petit prix (15eles 2,5m x 25mm). Les jonctions se font avec des L et des T en PVC. Si ce n'est pas assez rigide, je pourrais encore ajouter des équerres métaliques.

2.2 | L'électronique
2.2.1 | Spécication

L'électronique de commande doit respecter les spécications suivantes : Elle devra piloter 5 axes (1 X-axis, 1 Y-axis, 2 Z-axis, 1 extrudeur)
Elle se connectera à un ordinateur via le port USB
Elle supportera une carte SD pour l'imprimante soit autonaume lors
| de l'impression
Elle saura piloter des moteurs pas à pas bipolaires
Elle intégrera les diérents capteurs (n de course, températere de l'ex-
| trudeur)
Elle saura piloter le partie chauante de l'extrudeur
Elle ne sera pas propriétaire

4

2.2.2 La Smoothieboard

Toujours, pour des questions de budget, j'ai écarté la solution Smoothie (http ://smoothieware.org/smoothieboard). Il faut compter 125e pour une carte 5 axes.

### 2.3 Arduino

La solution Arduino consiste à utiliser la version Mega et y brancher une carte de commande de moteur. Je suis donc parti sur la conguration suivante :
Freeduino 2650 Mega (un clone de l'Arduino, mais en moins cher) : 19e RAMPS (une carte de commande de moteur ; la plus utilisée par les
| rmwares proposés) : 14e
5 modules A4988 (commande de moteur pas à pas) : 5e chacun
2.4 | Liste du matériel
| Description | Qte | Prix
1 | V modulaire | 6 | 6.60 e
2 | T modulaire | 2 | 2.80 e
3 | Tube alu modulaire 23.5 | 2.5 | 15.50 e
4 | Carte RAMPS | 1 | 14.00 e
5 | Commande moteur A4988 | 5 | 23.00 e
6 | Funduino 2650 Mega | 1 | 19.00 e
7 | Roulements linéaires LM8UU | 12 | 6.70 e
8 | Courroie GT2 (2m) + 2 poulies | 1 | 7.00 e
9 | Moteur pas à pas nema17 | 5 | 72.00 e
10 | Rond inox 8mm | 3 | 20.00 e
11 | Injecteur SD05447200 / SD05447000 | 1 | 2.00 e
12 | Alimentation PC 500W | 1 | 5.00 e
13 | Résistance 5.6(5W) / CTN 100k | 1 | 1.00 e
14 | Coupleur 5x8 | 2 | 2.00 e
15
16 | Total | | 196.60 e

5

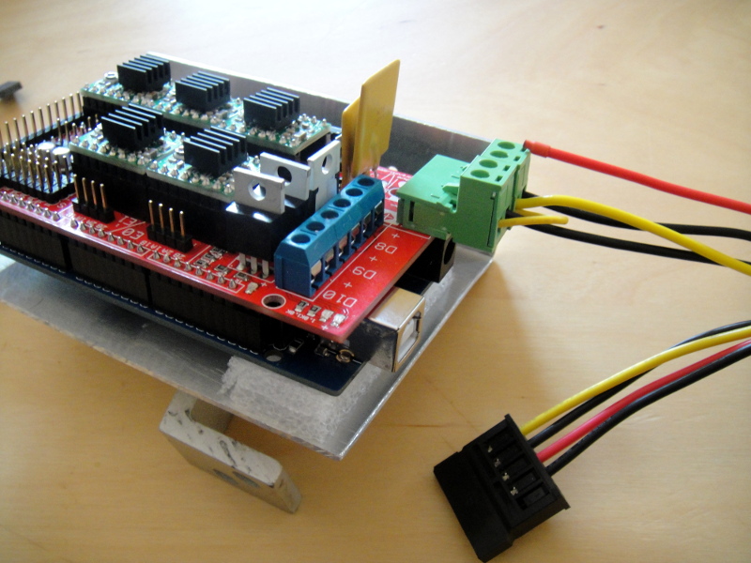
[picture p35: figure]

Figure 2: Montage de RAMPS sur la Funduino

3 | Mise en oeuvre
3.1 | L'électronique
3.1.1 | Un jeu de LEGO

Le montages erst relativement simple ; la carte RAMPS s'enche bien sur la Funduino. Il ne faut pas assembler tout de suite les cartes. Il est préférable de xer la funduino sur son support nal (dans mon cas, une tole aluminum en équerre). une fois le Funduino xée, on enche la RAMPS (g. 2 page 6). il reste à brancher les commandes de moteur sur la RAMPS. Comme indiqué sur le wiki de Reprap, on vérie les nom des broches et on branche (le GND va sur le GND et le direction va sur direction).

3.1.2 Alimentation externe

Il faut maintenant l'alimentation externe sur la RAMPS (bornier vert à quatre broches). Il est préconisé d'alimenter en 12V. J'ai donc utilisé une alimentation de PC (500W, qui peut le plus, peu le moins). Pour info, le 0V, c'est le l noir, le 12V, c'est le l jaune. Comme d'habitude, l'alimentation de PC est un élément que j'ai trouvé dans un vide-grenier (5e). Il y a une entrée 5A et une entrée 11A. Mon alimentation a une capacité de 18A sur la sortie 12V. Il m'a donc sut de mettre les deux entrées en parallèle sur le 12V g. 3 page 7).

6

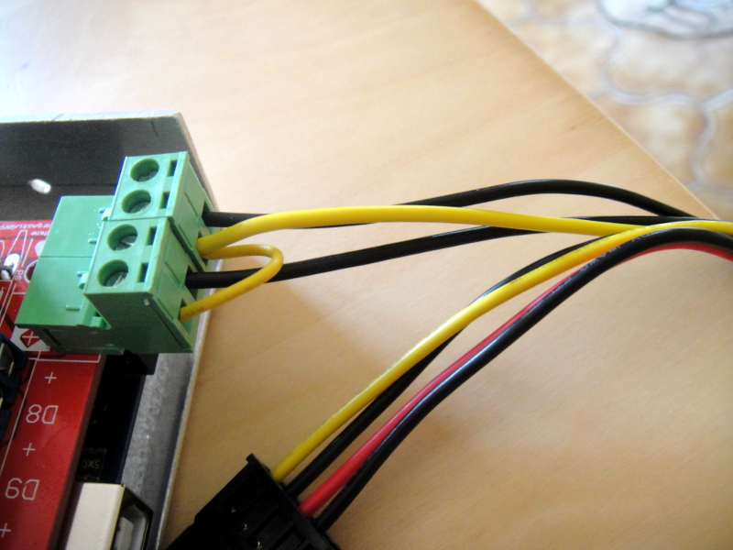
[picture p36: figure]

Figure 3: Branchement de l'alimentation externe

3.1.3 Les premières embuches

Ce qui devait arriver arriva. En faisant des essais sur la carte RAMPS, j'ai fait un court-circuit. Une seconde a sut pour que de la fumée s'échappe de la Funduino. Une fois l'ensemble démonté, un composant avait pris copieux. Diagnostique : quand je branche seule, le Funduino au PC avec le cordon USB, le périphérique est reconnu. Si maintenant, j'alimente la RAMPS en 12V, le PC perd la connection USB. C'est embêtant. Dans ces cas là, il faut garder son calme. La Funduino, tout comme l'Arduino est une carte super simple : il y a un micro controlleur, quelques résistances, un condensateur, parfois une interface USB (sinon, pris en charge par le micro controlleur), et ... un régulateur de tension (AMS1117). Ce régulateur de tension permet de garder 5V dans le circuit quelque soit la tension d'alimentation (tant qu'elle reste au dessus de 5V). C'est un composant à trois pattes équipé d'un radiateur, qui ressemble à une quatrième patte (g. 4 page 8). En regardant bien, c'est ce composant qui a chargé. La réparation est simple : le LM7805 rempli la même fonction. Il est carément plus gros, mais, on va trouver à le loger. J'en ai un sous le coude, c'est parti. Il faut être vigilent sur l'ordre des pattes. Pour s'adapter sur le circuit, il faut croiser le OUT et le GND pour avoir dans l'ordre [IN OUT GND] (g. 4 page 8). Ensuite on soude (g. 5 page 8). J'ai pris soin de mettre un scotch sur le radiateur du LM7805 pour éviter que la partie métallique ne touche une autre partie de la Funduino. Je rebranche le tout, et ... c'est reparti comme en 40 ! Ce qu'il faut retenir, c'est que la Funduino est très fragile (en même temps, un court-circuit ne

7

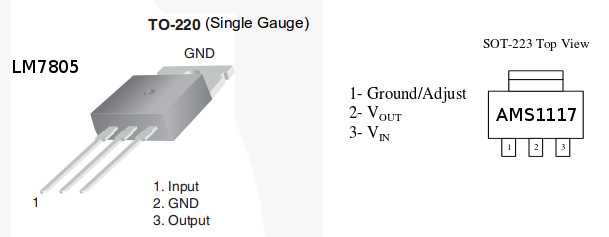
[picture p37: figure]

Figure 4: Régulateurs de tension

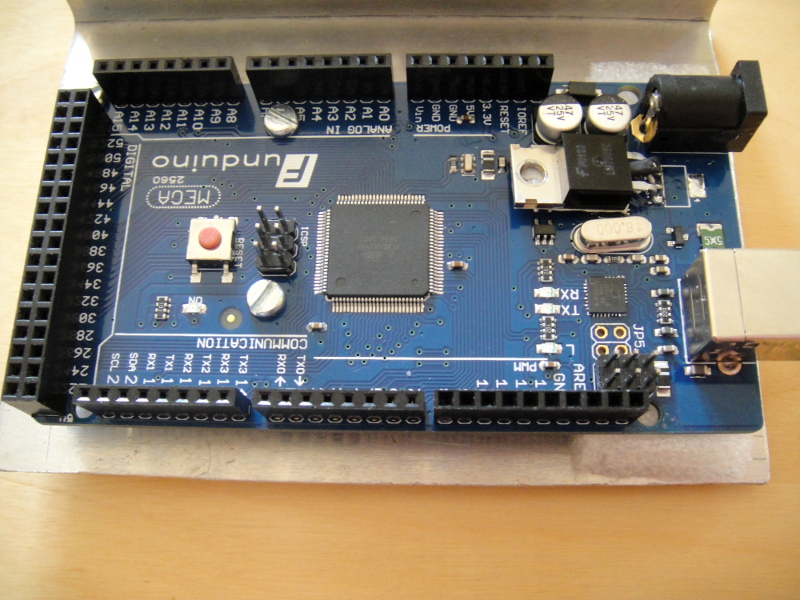
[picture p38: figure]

Figure 5: Funduino avec son nouveau régulateur de tension

pardonne pas), et qu'il faut vérier à deux fois avant de brancher quelque chose (on ne branchera rien à chaud !).

8
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

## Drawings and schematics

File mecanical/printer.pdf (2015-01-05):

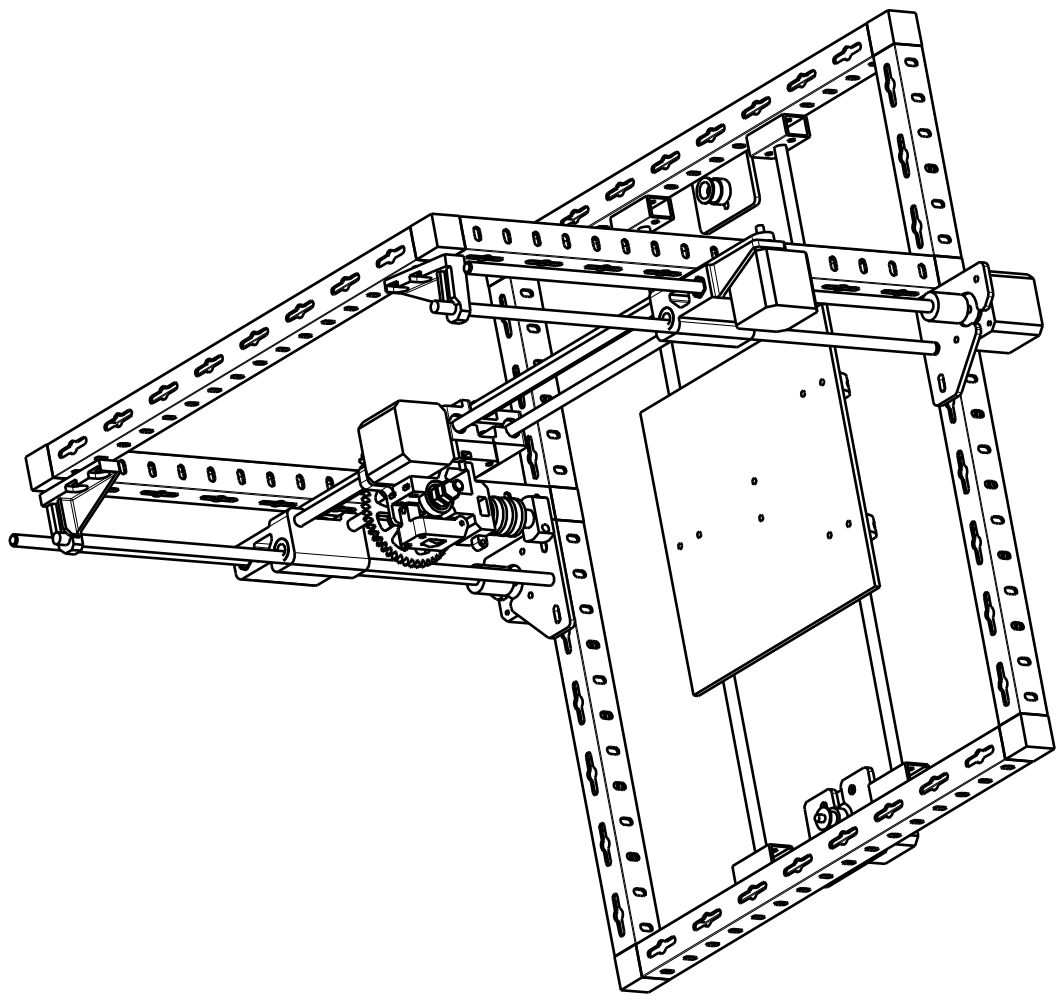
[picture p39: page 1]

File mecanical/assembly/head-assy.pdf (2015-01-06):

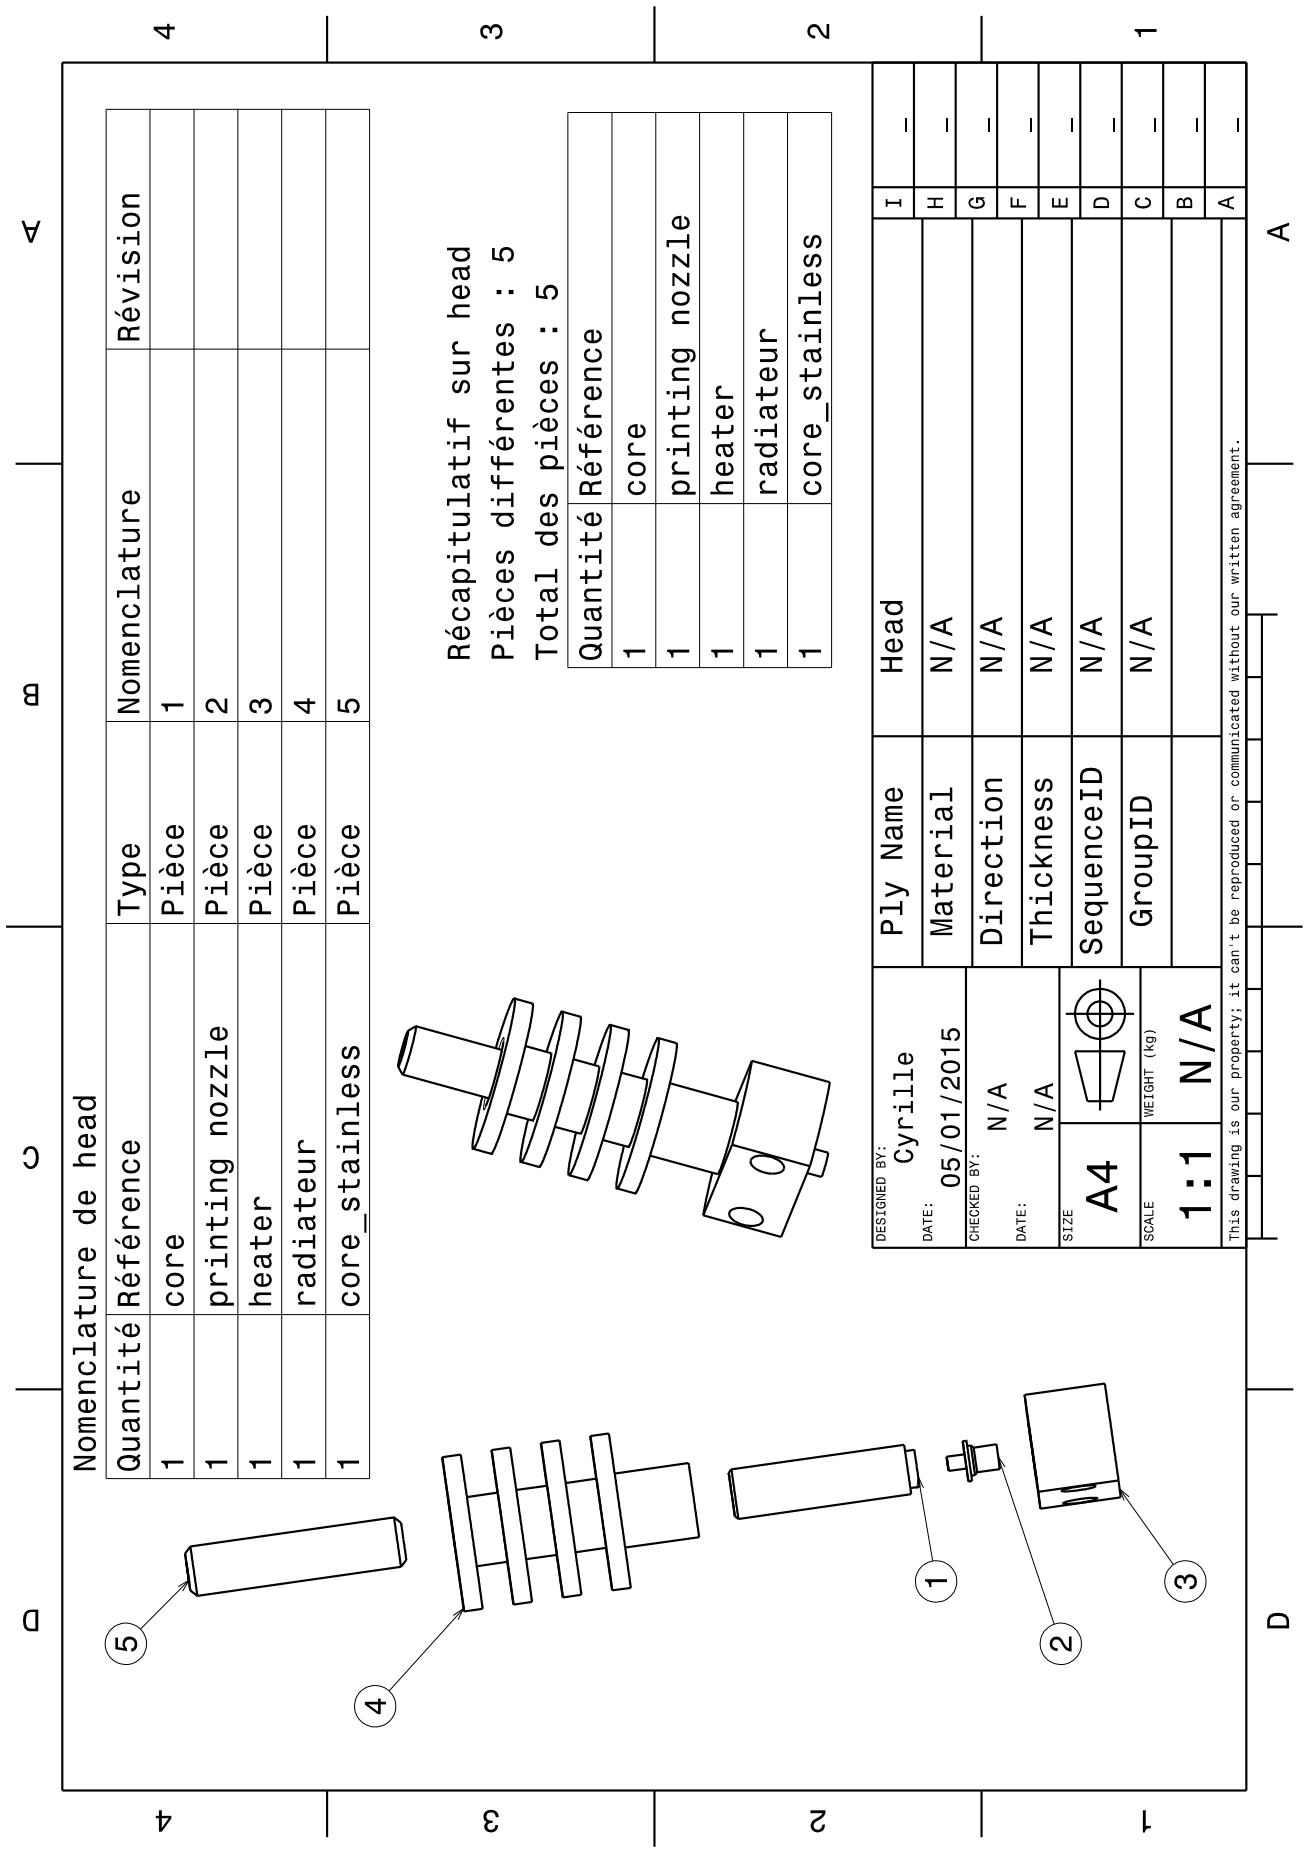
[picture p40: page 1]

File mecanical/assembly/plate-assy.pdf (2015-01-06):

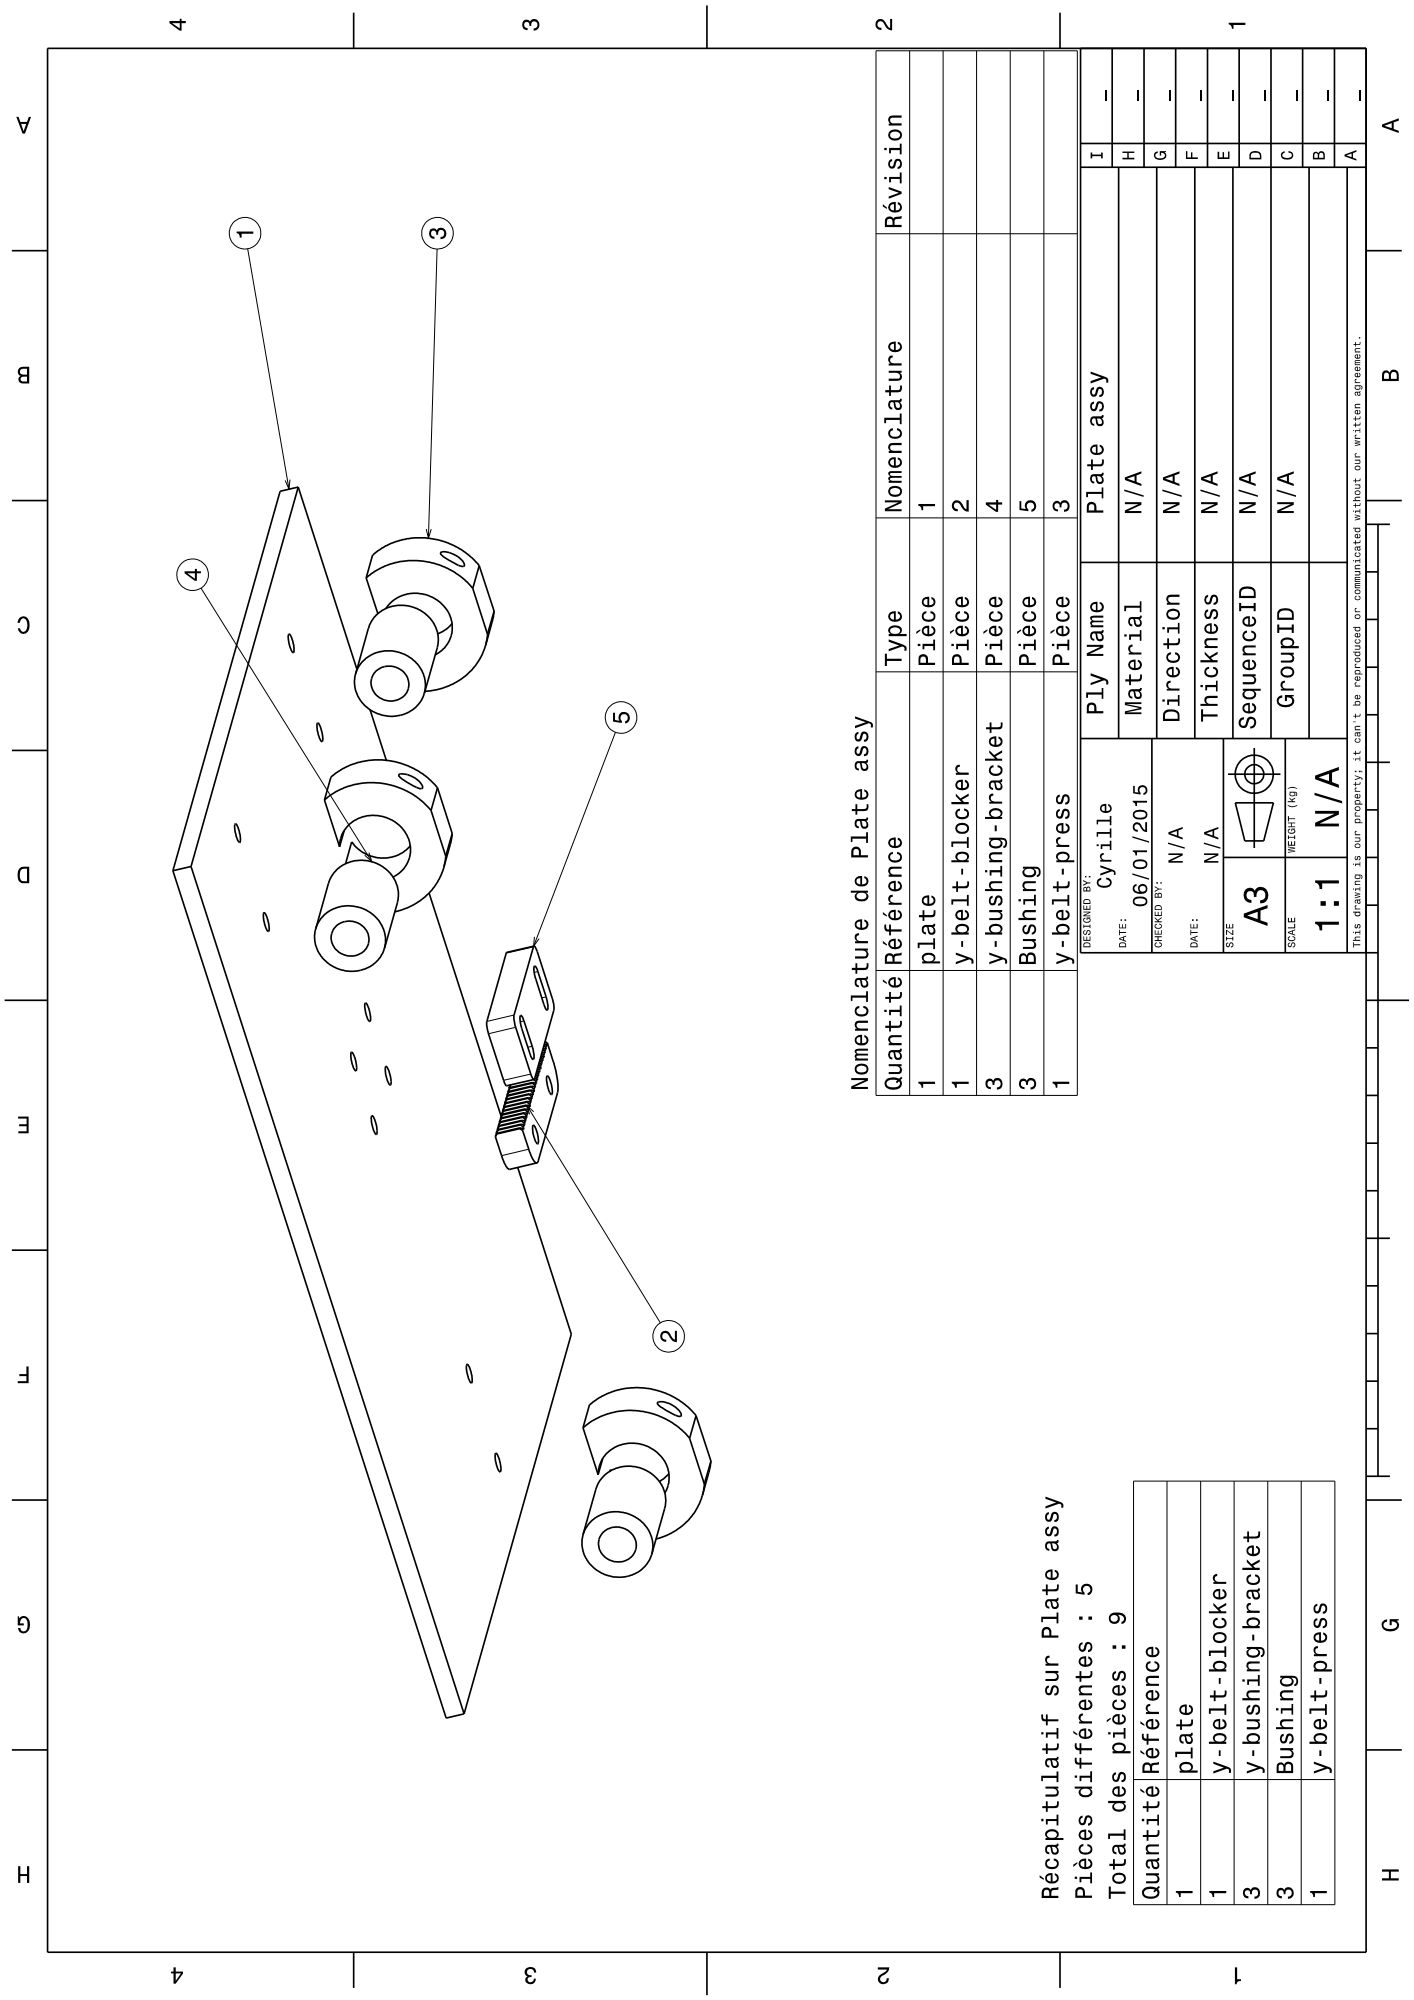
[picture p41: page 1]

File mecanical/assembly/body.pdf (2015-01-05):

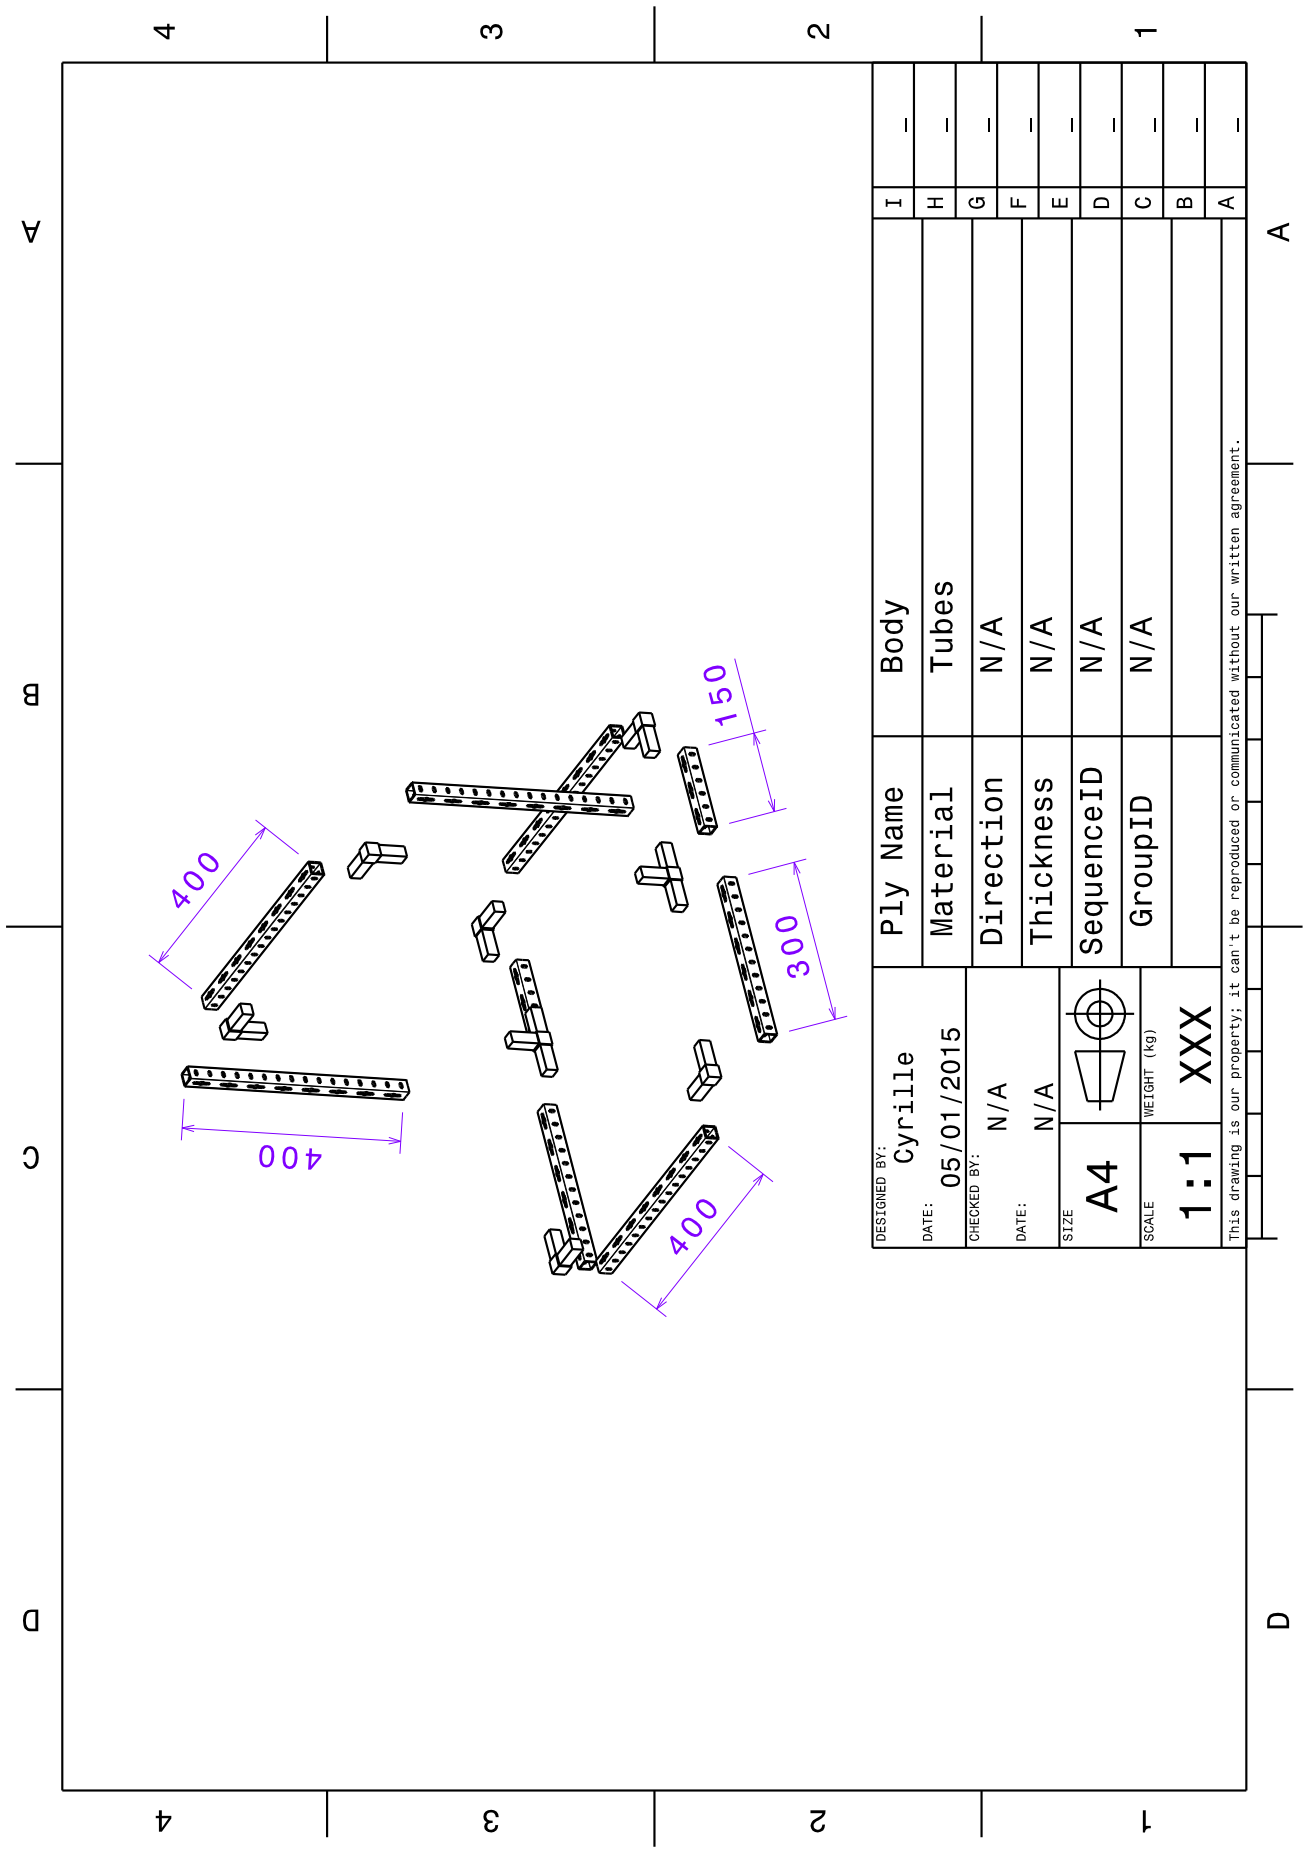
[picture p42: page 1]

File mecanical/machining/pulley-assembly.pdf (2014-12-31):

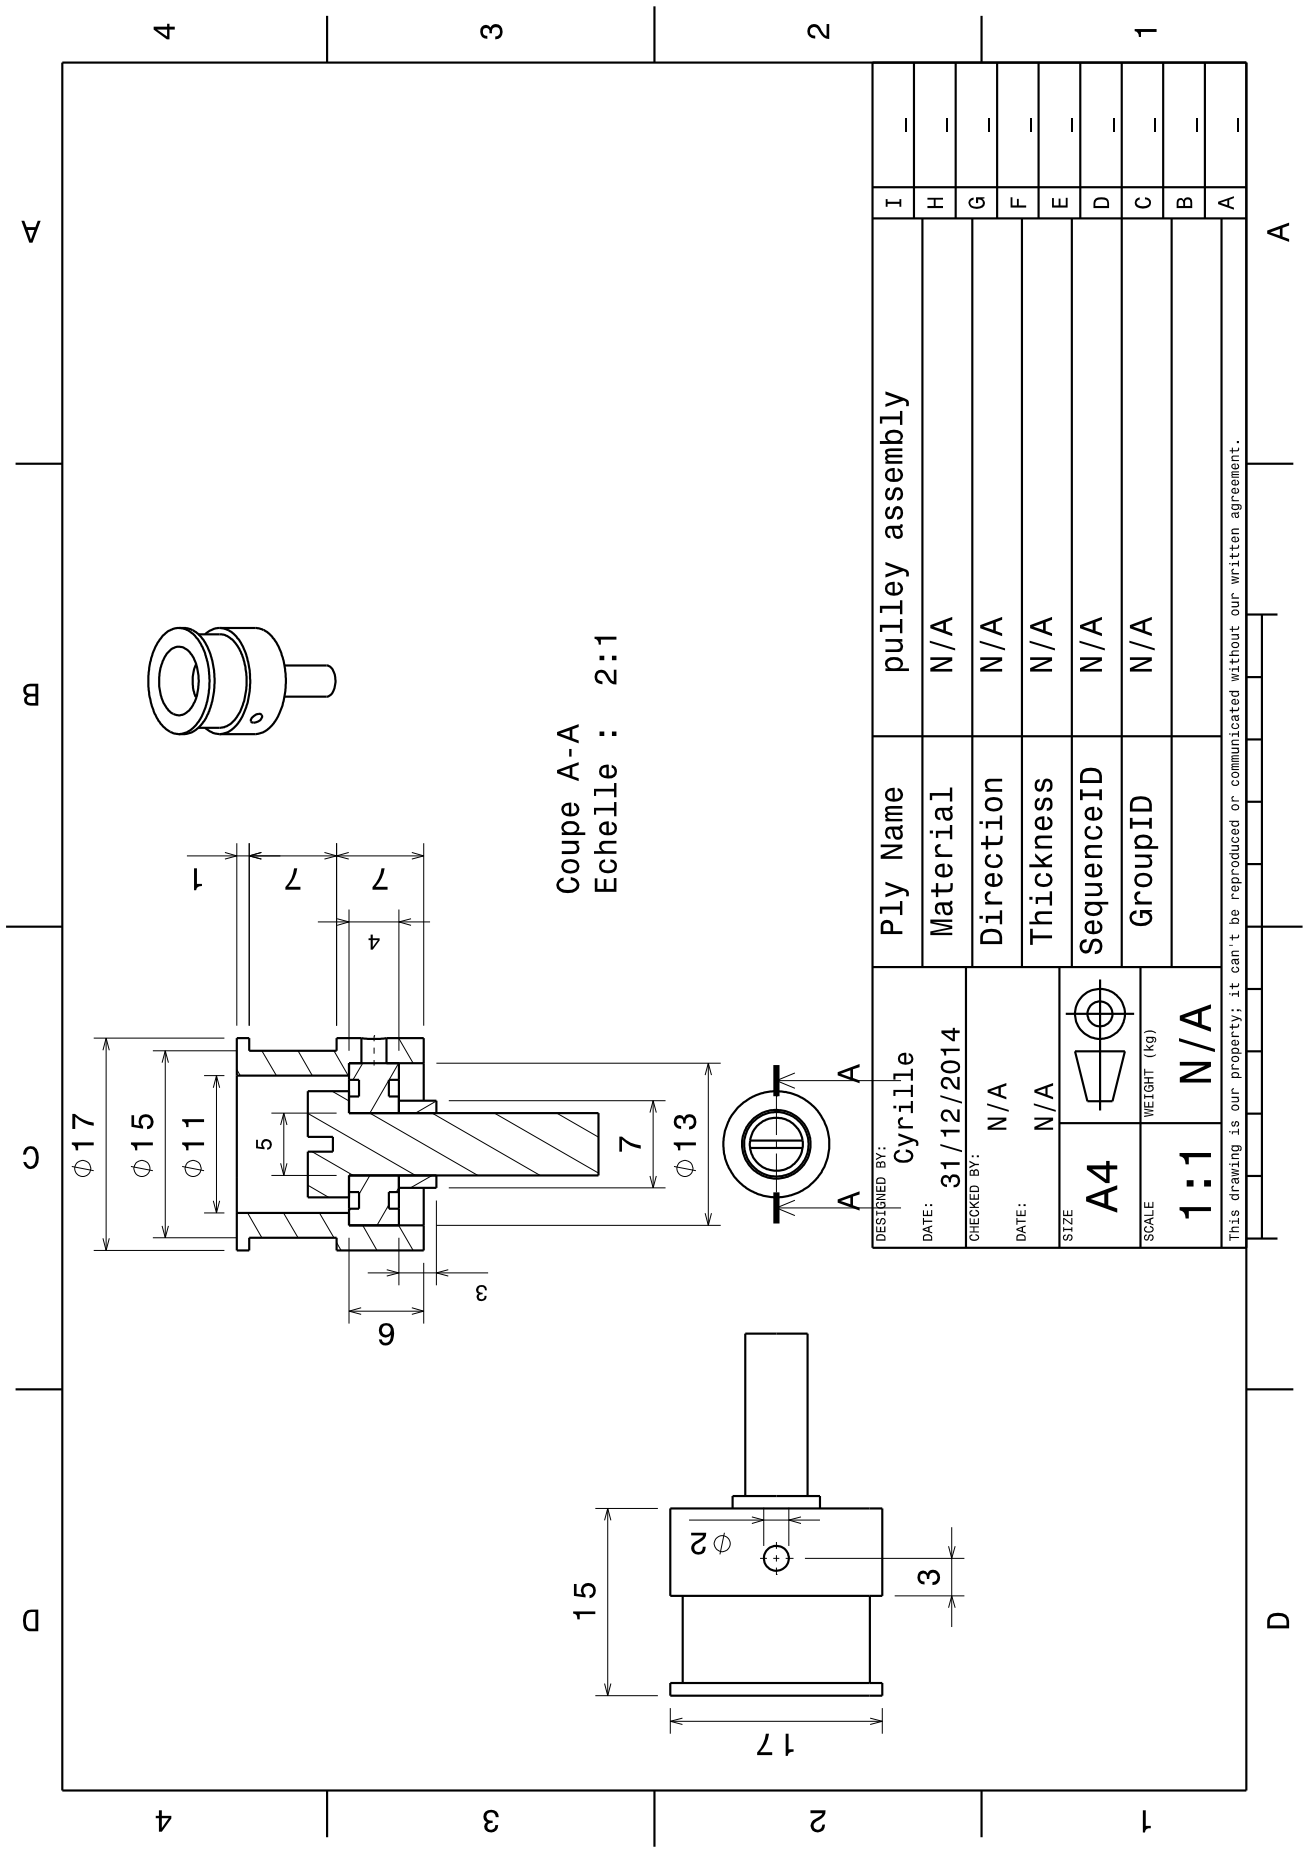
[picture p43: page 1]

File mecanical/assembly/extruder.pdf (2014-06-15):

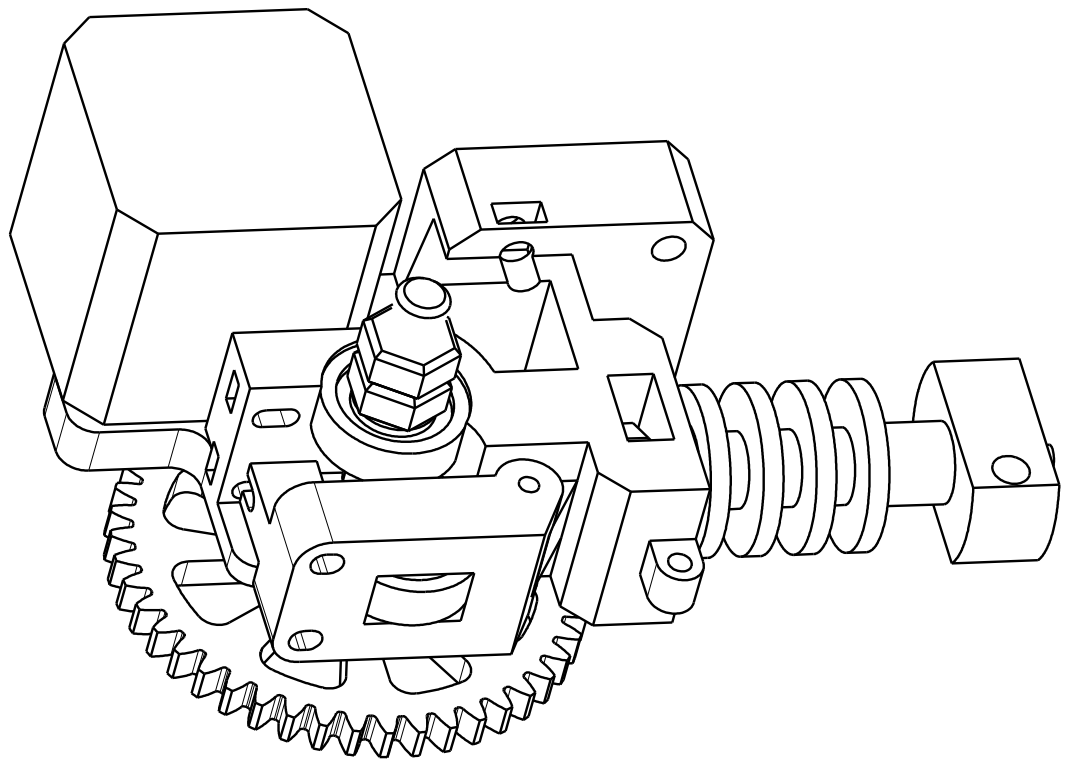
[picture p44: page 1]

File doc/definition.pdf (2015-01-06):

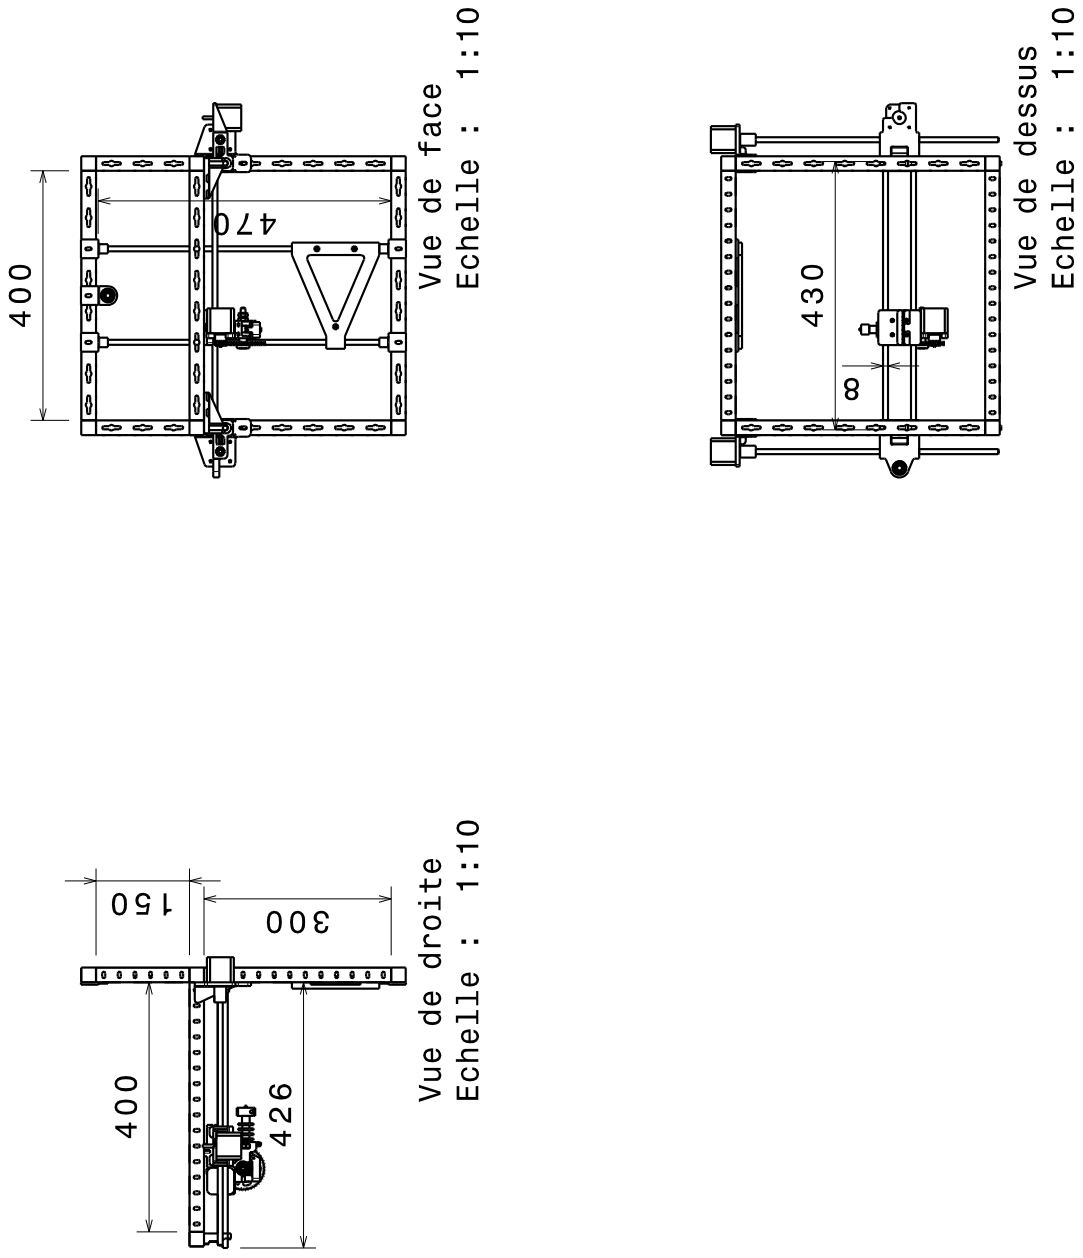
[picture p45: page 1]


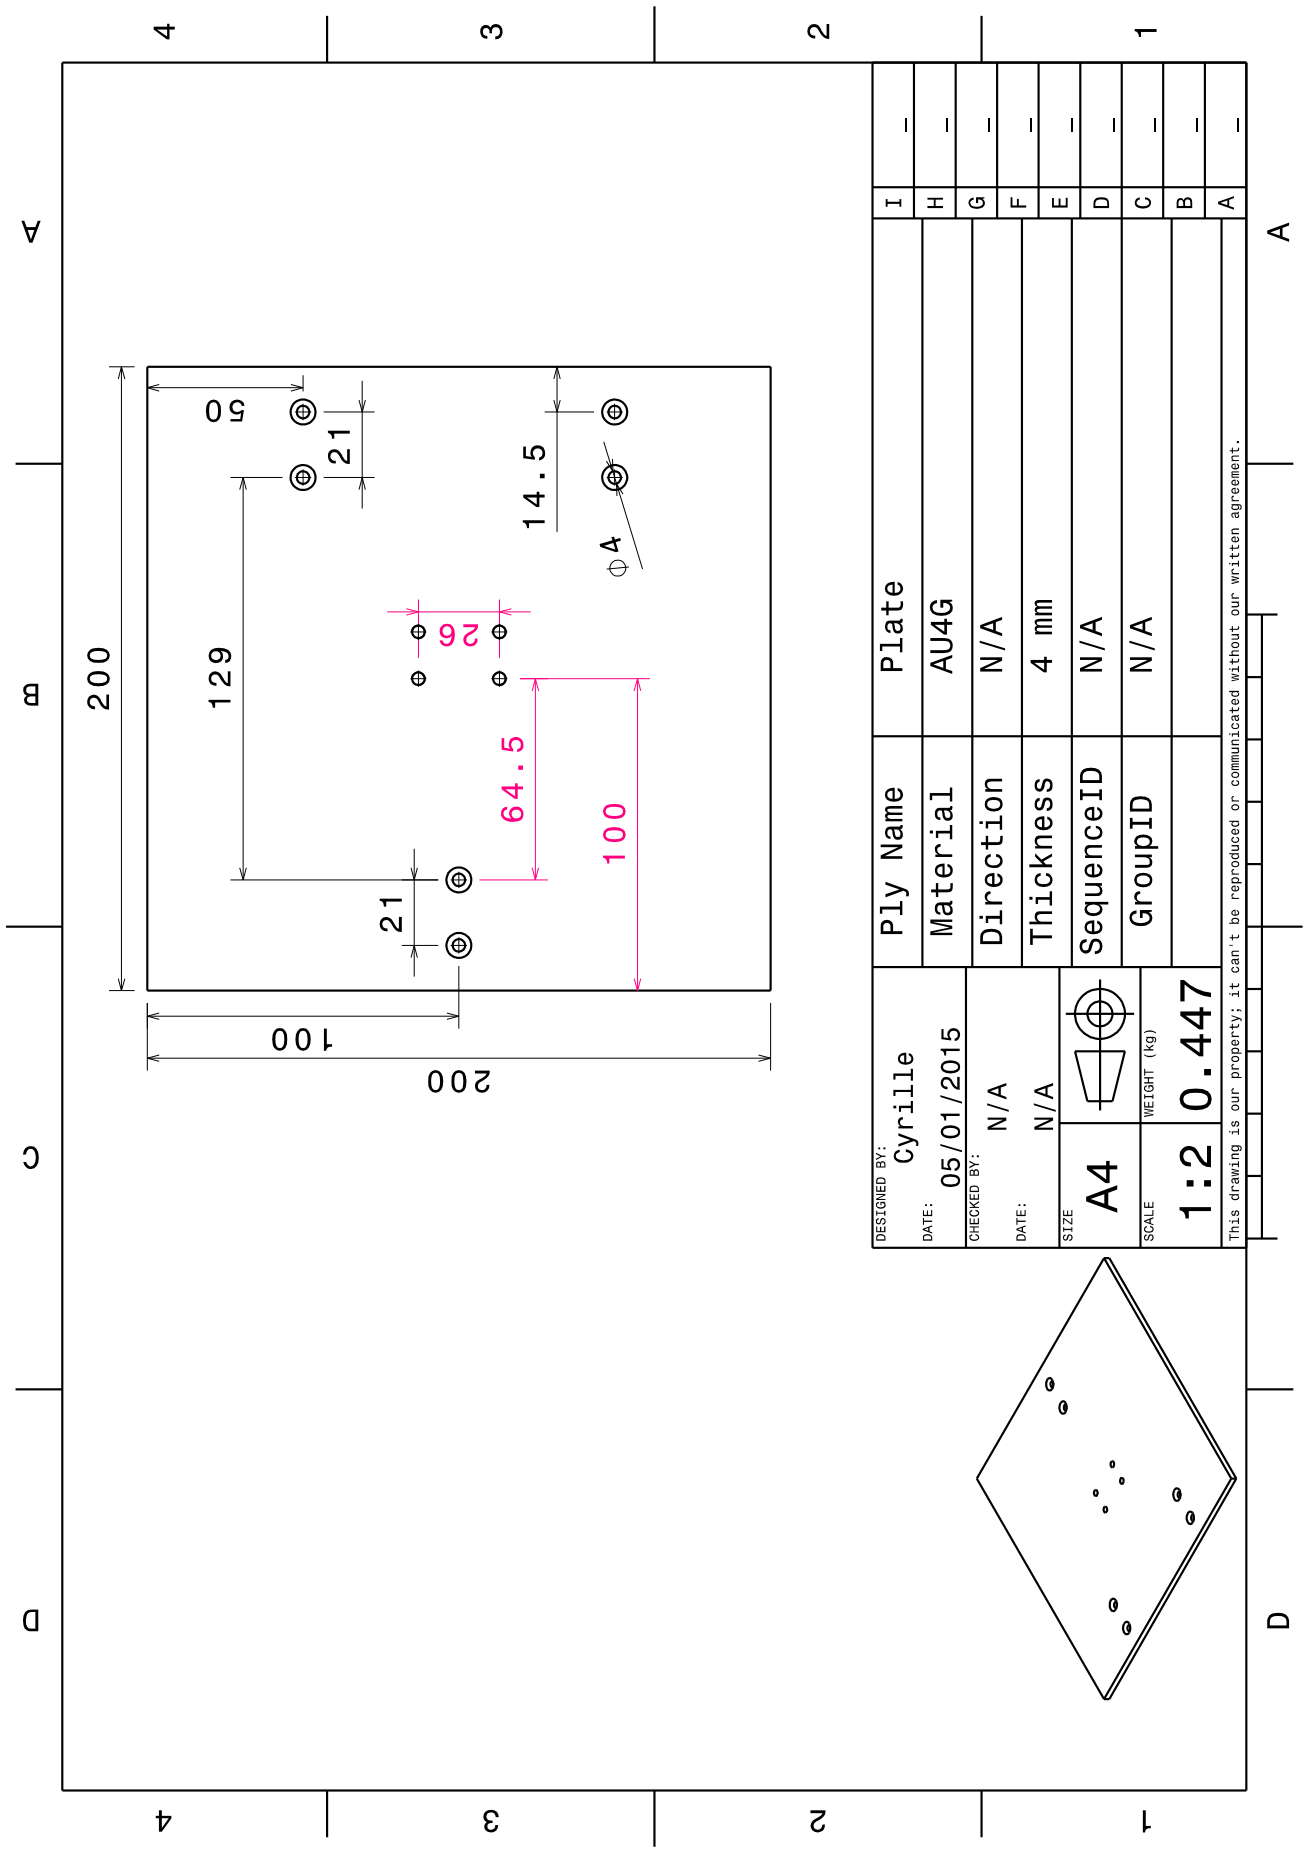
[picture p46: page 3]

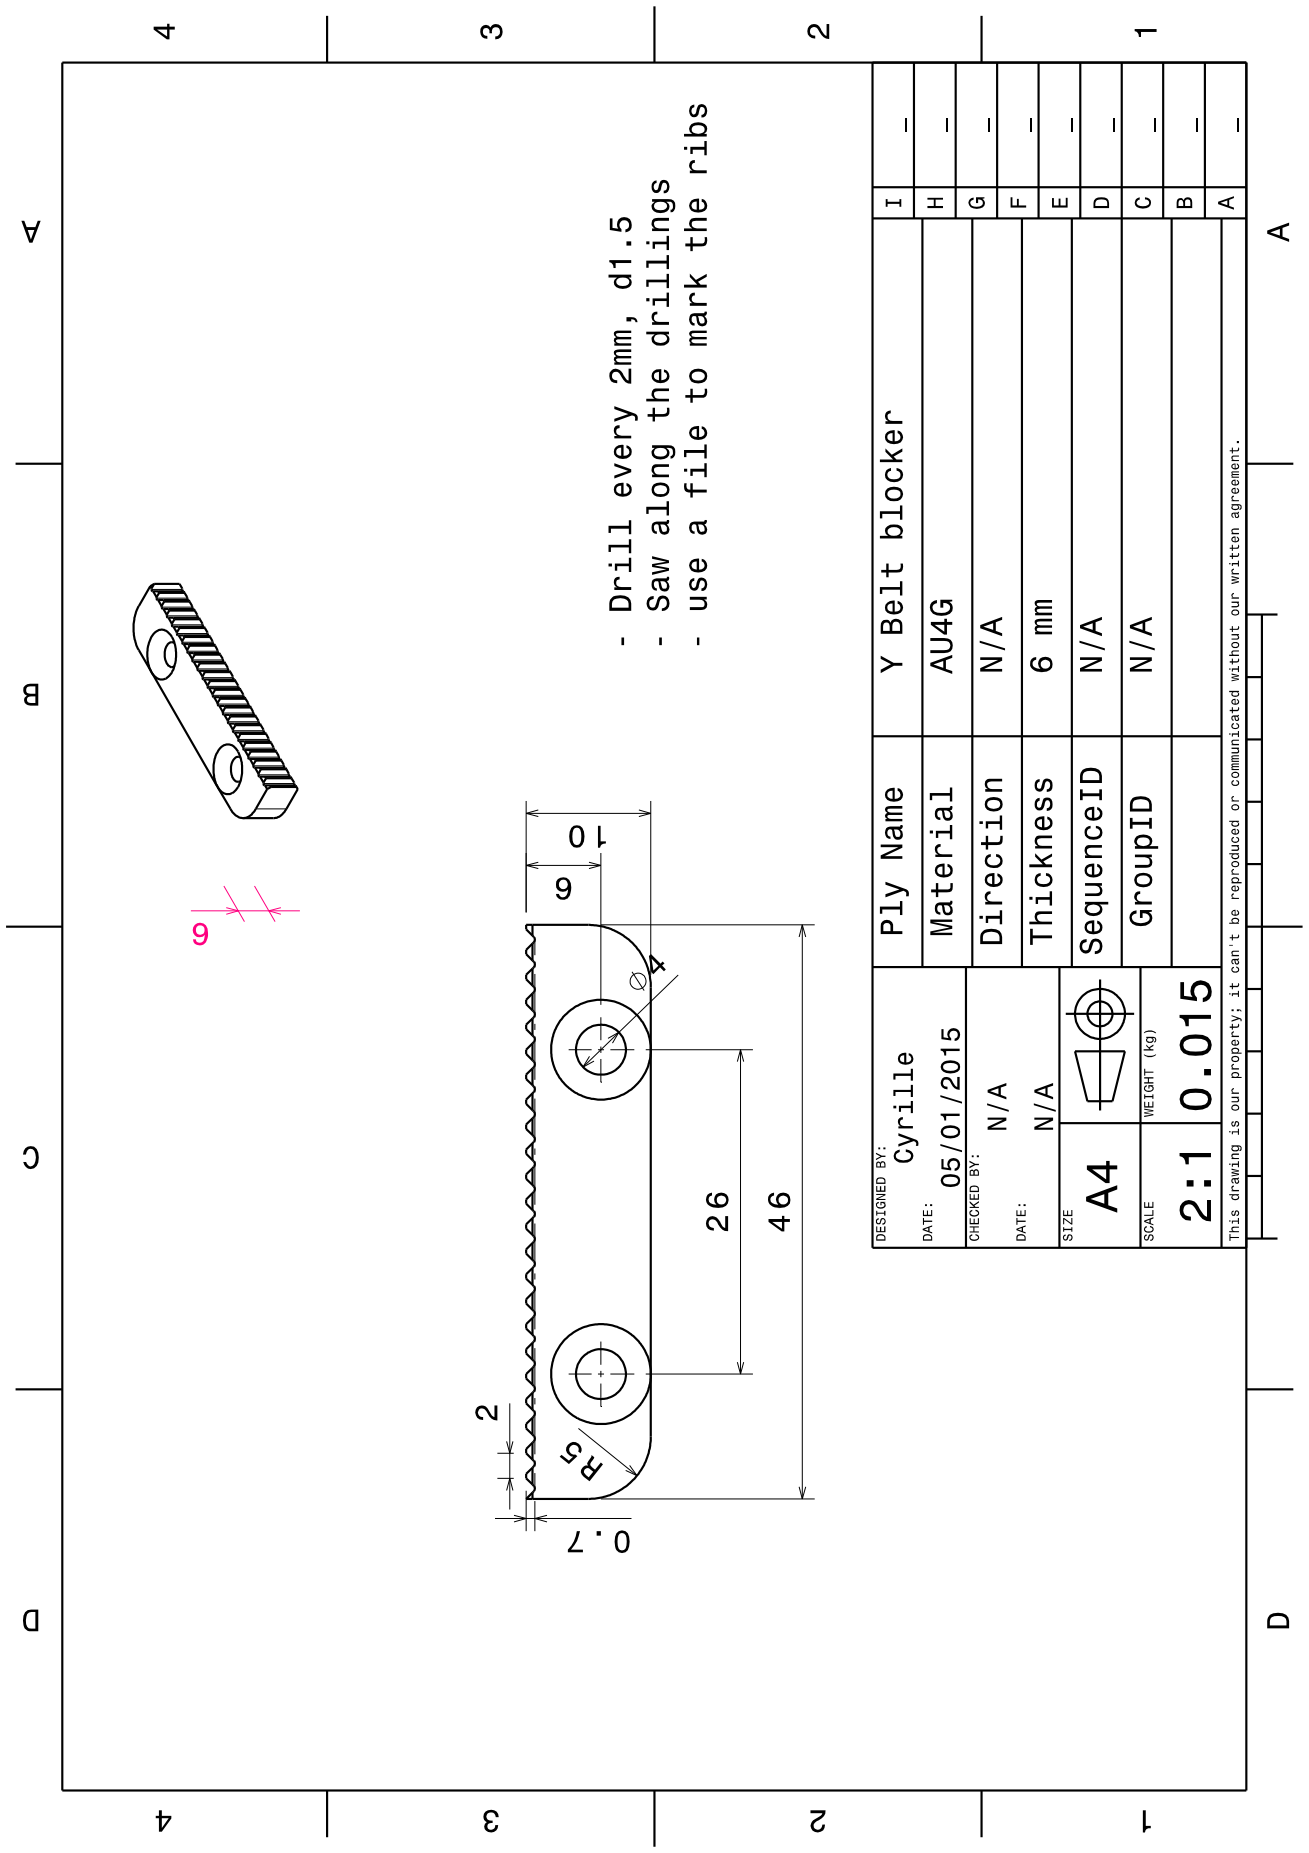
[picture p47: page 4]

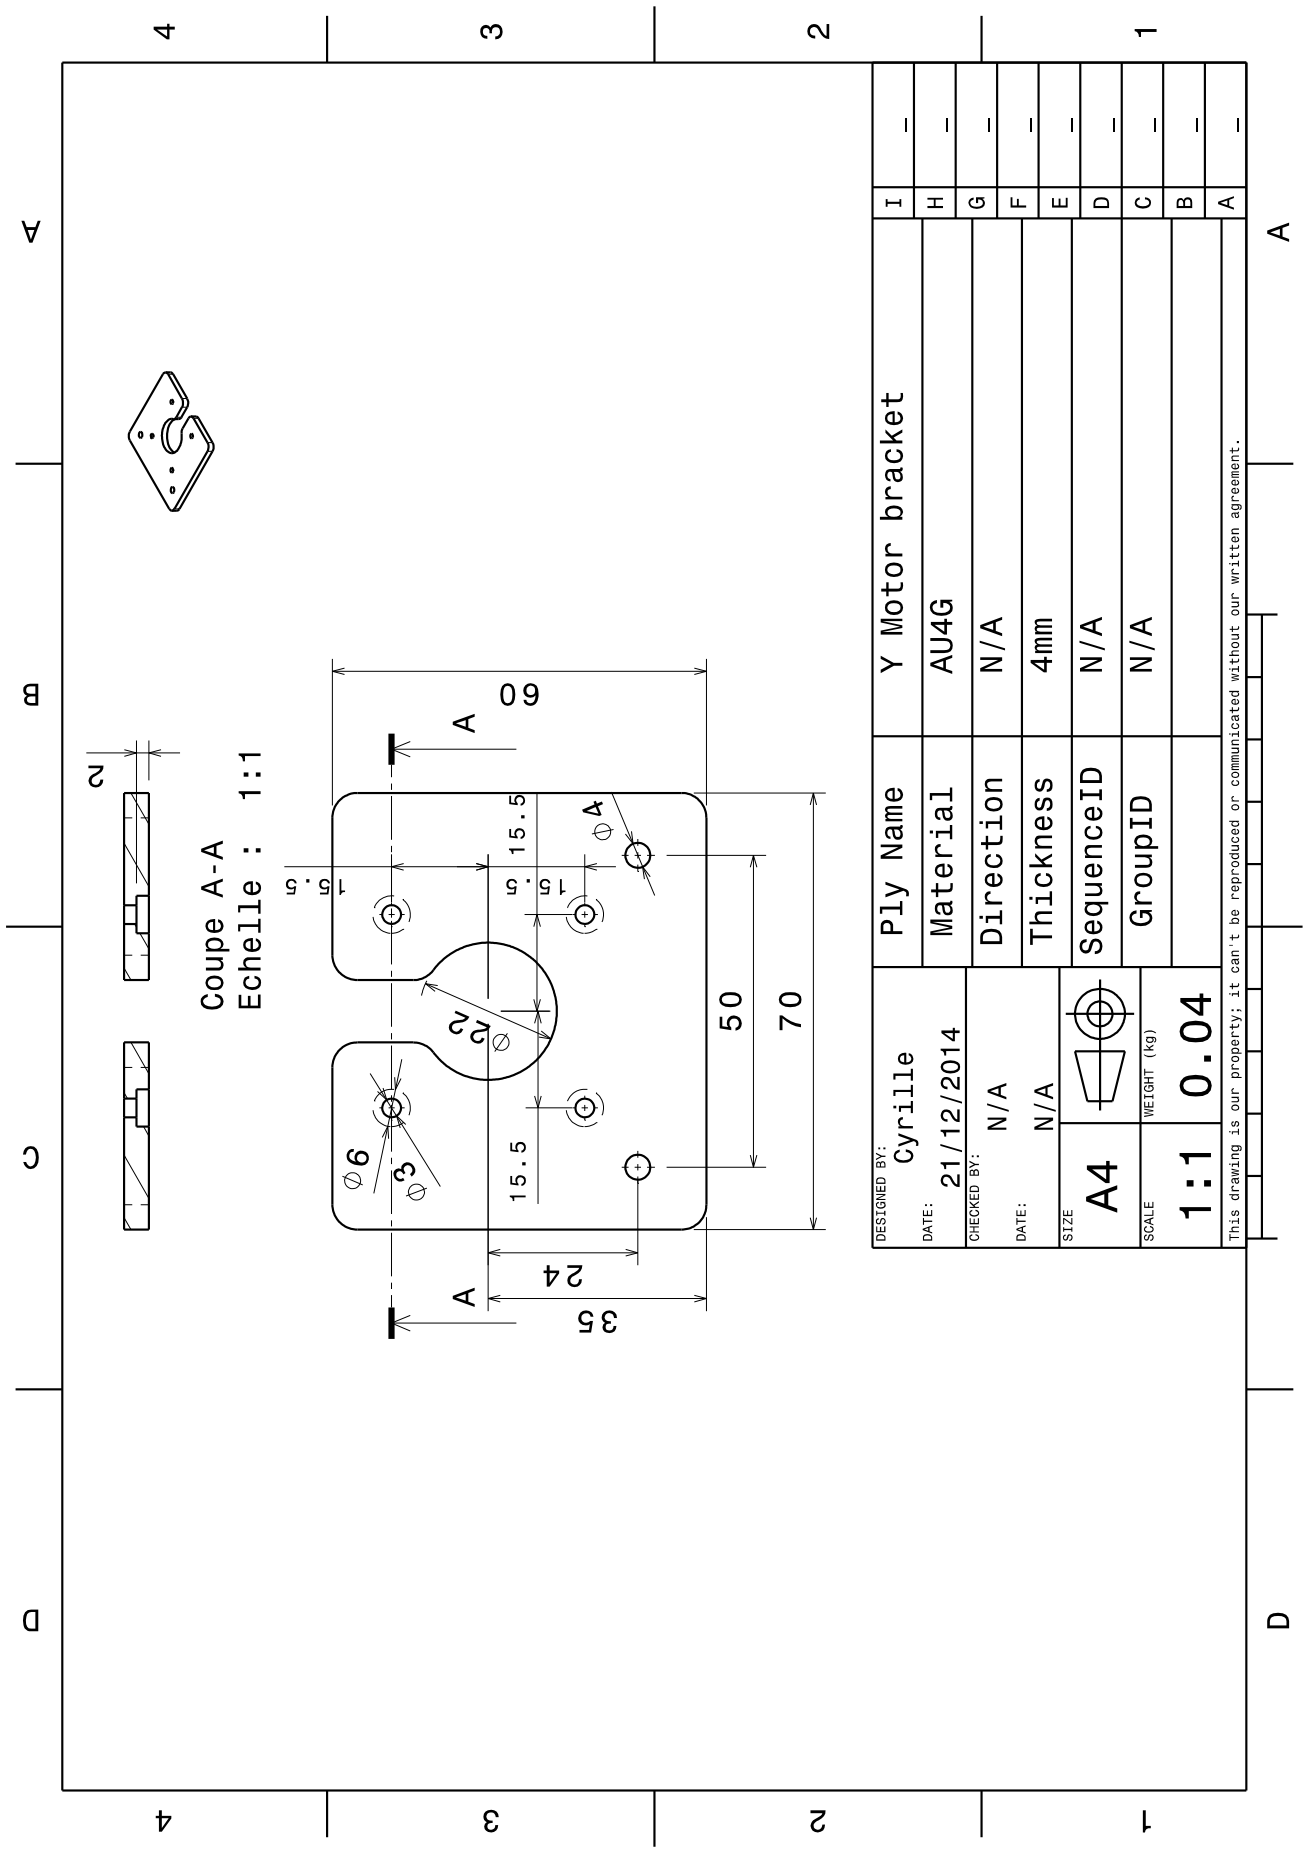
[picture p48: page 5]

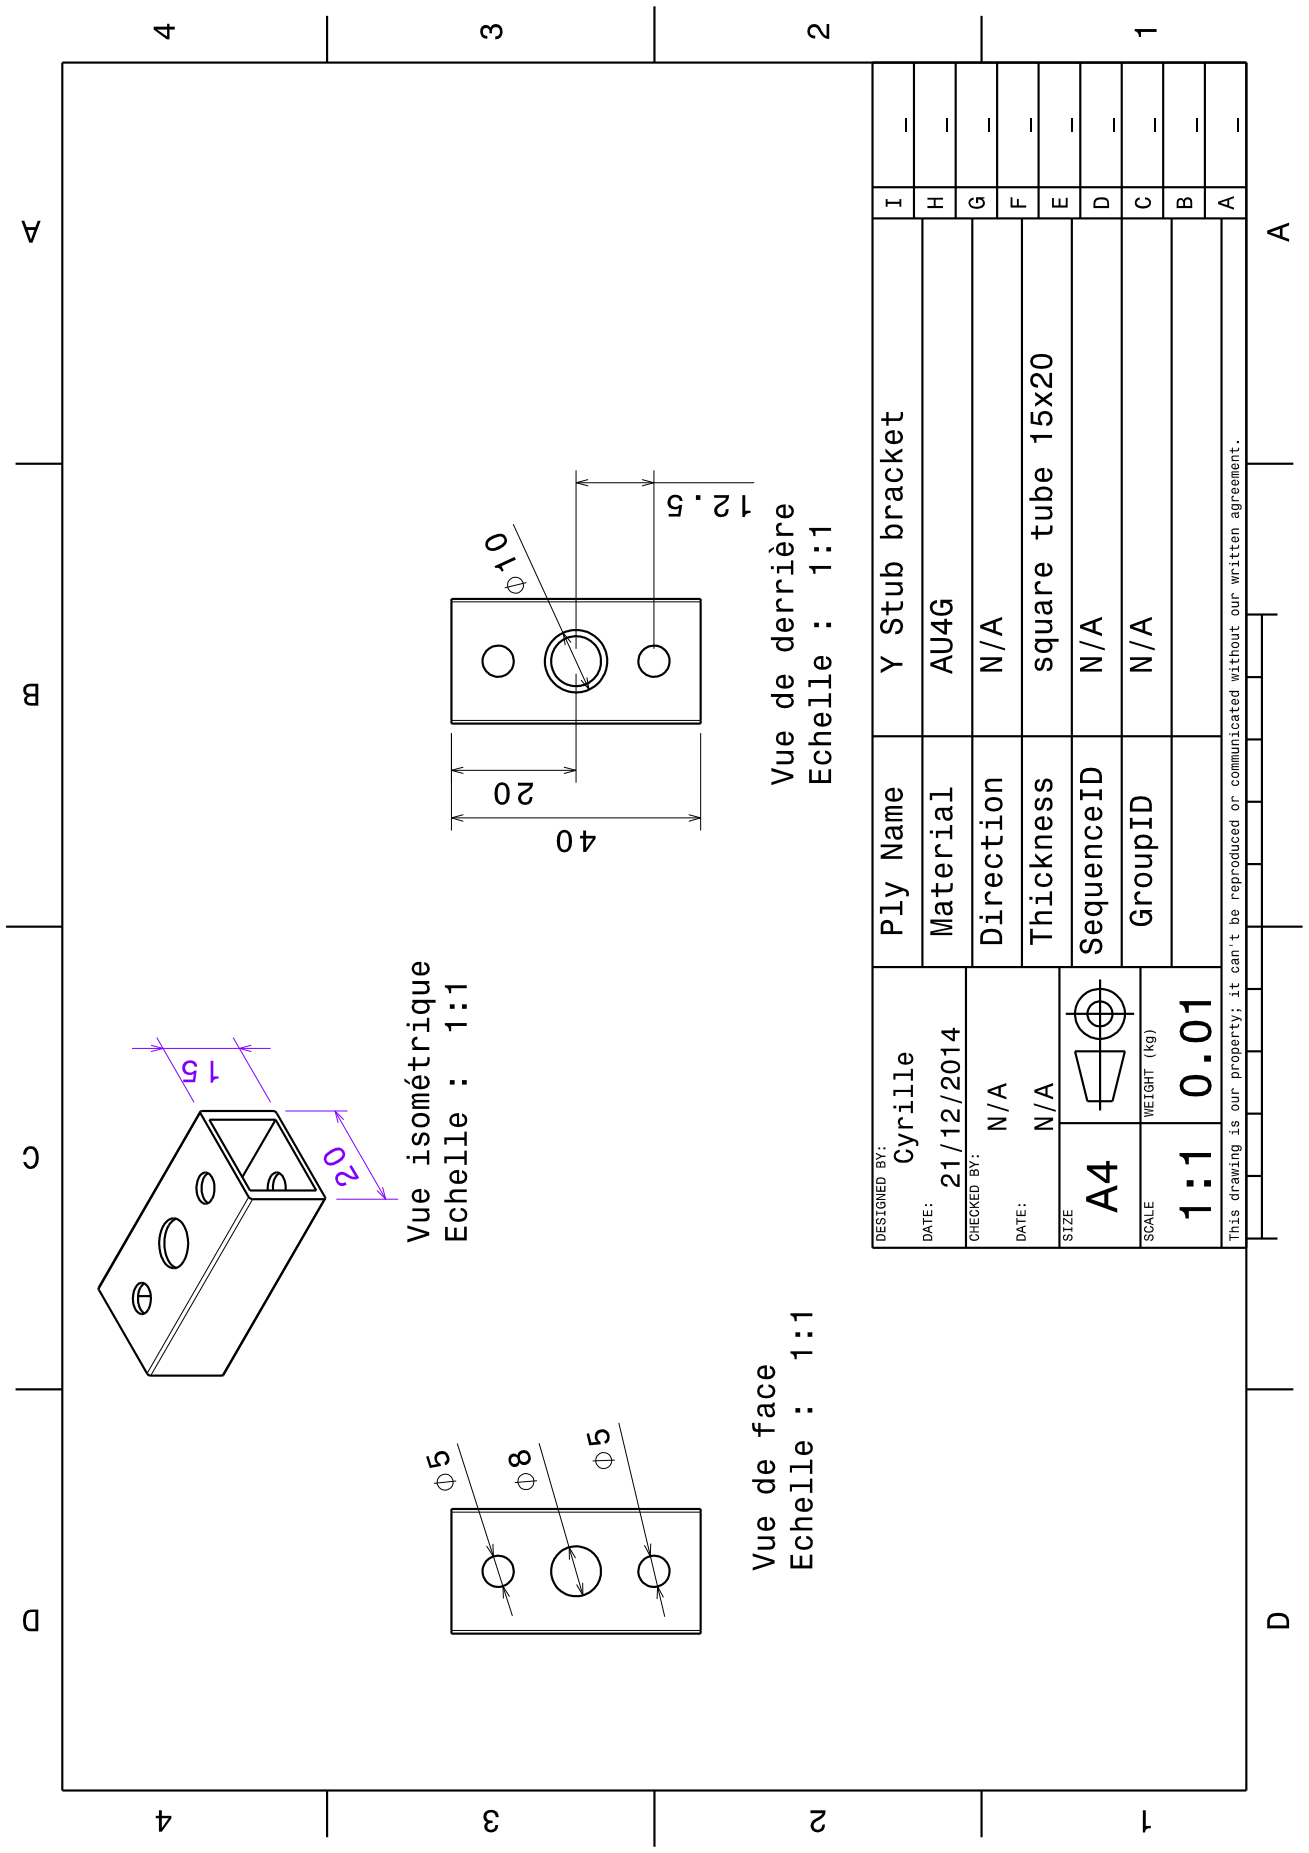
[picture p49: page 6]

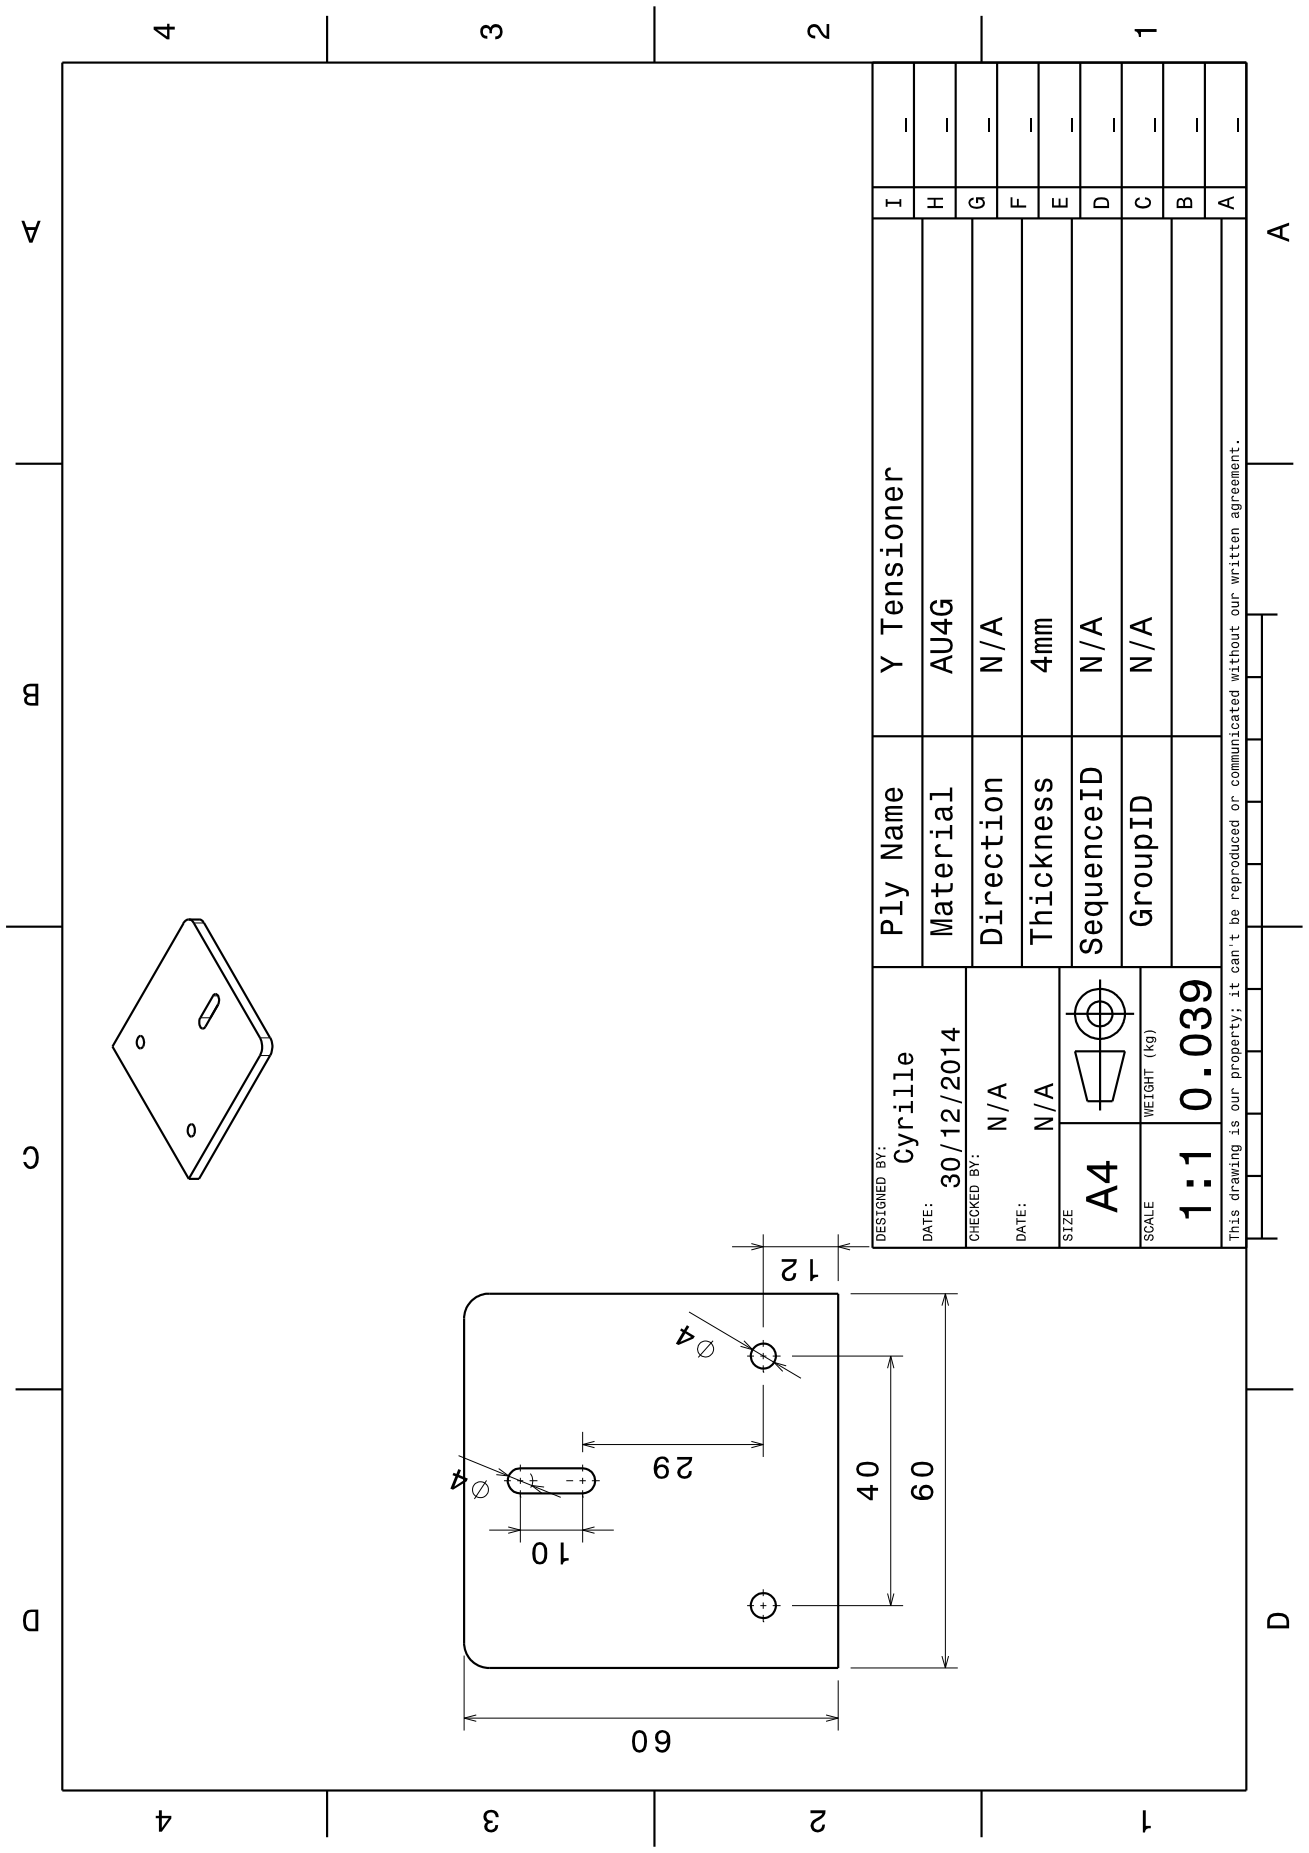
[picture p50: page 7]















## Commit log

2014-06-06 doc update
    [Motor-Support-bottom-left.stl, Motor_Support_bottom_right.stl]
2014-06-06 sync commit
    [heater.CATPart]
2014-06-07 Z-carriage
    Optimize the file structure
    [ARDUINO-WASHER.stl, BODY-EXTRUDEUR-WADE-1.75mm-with-support.stl, BODY-EXTRUDEUR-WADE-with-support.stl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]
2014-06-08 reorganize assemblies
    [L.CATPart, L.stl, Stub_Y.CATPart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]
2014-06-09 Arduino principle in doc
2014-06-09 Gears for extruder
    [Motor.CATPart, Z_carriage_left.stl, big_gear.CATPart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]
2014-06-11 bearings and extruder bracket
    [Motor-Support-bottom-left.CATPart, Motor-Support-bottom-left.stl, Motor.CATPart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]
2014-06-12 Printing head in main assembly
    [bearing.CATPart, bearing02_10.CATPart, bearing02_12.CATPart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]
2014-06-14 Z carriage
    [Z-Axis-Top-Left.CATPart, Z-Axis-Top-Left.stl, Z-Axis-Top-Right.CATPart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]
2014-06-14 Z-carriage offset and re-center printing head
    [Motor-Support-bottom-left.CATPart, Motor_Support_bottom_right.CATPart, Stub_Y.CATPart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]
2014-06-14 STL part update
    [Motor-Support-bottom-left.stl, Motor_Support_bottom_right.stl, Z-Axis-Top-Left.stl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]
2014-06-15 Extruder update
    [Produit1.CATProduct, bearing10_8.CATPart, core_stainless.CATPart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]
2014-06-16 X-carriage rework
    [X_Carriage.CATProduct, X_carriage.CATPart, X_carriage.stl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]
2014-07-02 picture of the printer in the readme file
2014-12-17 motor bracket
    [Motor-bracket.CATPart]
2014-12-17 Resize motor bracket
    [Motor-bracket.CATPart]
2014-12-21 Motor bracket made of au4g
    [Motor-bracket.CATPart, motor-bracket2.CATPart, stub-bracket.CATPart]
2014-12-29 bushing bracket for the plate
    [bracket-assembly.CATProduct, bracket.CATPart, screw.CATPart]
2014-12-31 tensioner assy and bracket drawing
    [pulley.CATPart, pulley.CATProduct, tensioner.CATPart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]
2015-01-05 Cleaning !
    [Motor-bracket.CATPart, X_Carriage.CATProduct, body.CATProduct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]
2015-01-08 z stub bracket in AU4G
    [X_Carriage.CATProduct, extruder.CATProduct, printer.CATProduct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]
2015-01-08 z-stub bracket reworked
    [z-stub-bracket.CATPart]
2015-01-08 Gear reworked to be printable
    [big_gear.CATPart, big_gear.stl]
2015-01-08 bushing bracket improvment
    [y-bushing-bracket.CATPart]
